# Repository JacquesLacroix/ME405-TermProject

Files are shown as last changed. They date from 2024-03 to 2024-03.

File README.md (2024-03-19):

<h1>ME 405 Term Project</h1>
<h3>Scott Frizzell & Jacques Lacroix</h3>

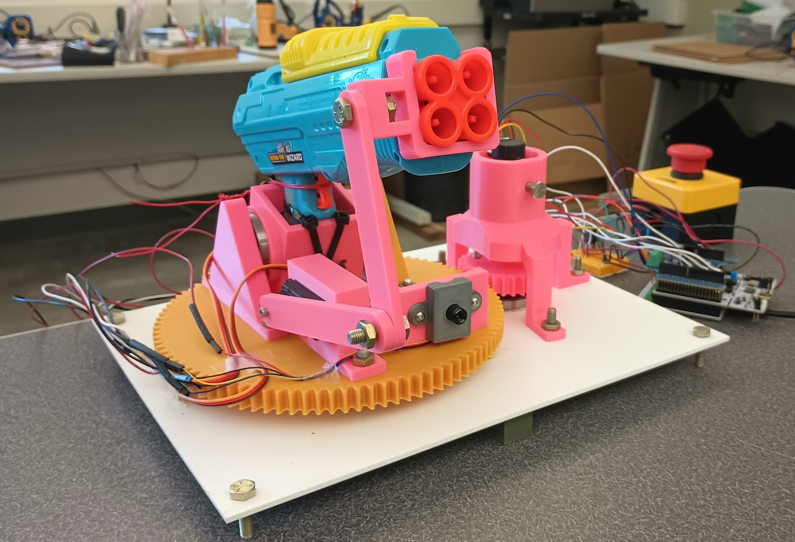
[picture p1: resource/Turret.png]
Picture of Turret


This thermal tracking, automated NERF™ turret was designed for the Department of Foamland Security. Its primary purpose is to engage in autonomous defense.

The turret's design revolves around a pump-action NERF™ gun mounted to a 2-axis mount, allowing it to shoot in nearly any direction. The mechanism uses a brushed DC motor to control the panning motion of the gun, while a servo controls the tilting motion of the gun. A servo is used to actuate the trigger mechanism, and a thermal camera is used for tracking.

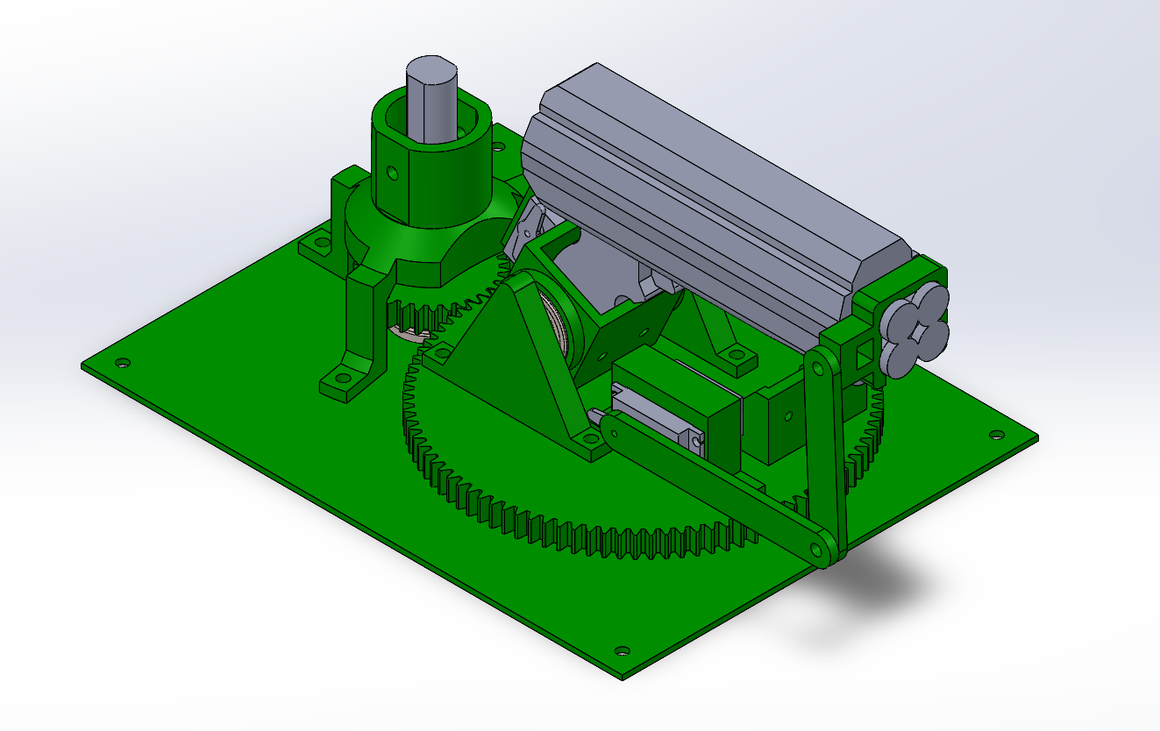
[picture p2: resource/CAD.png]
CAD model of Turret


The turret uses a gear train to reduce the motor speed and increase torque to allow the gun to swivel smoothly. Multiple tooth ratios were considered, such as 120/30, but we choose a 96/30 tooth ratio because of manufacturing constraints. 

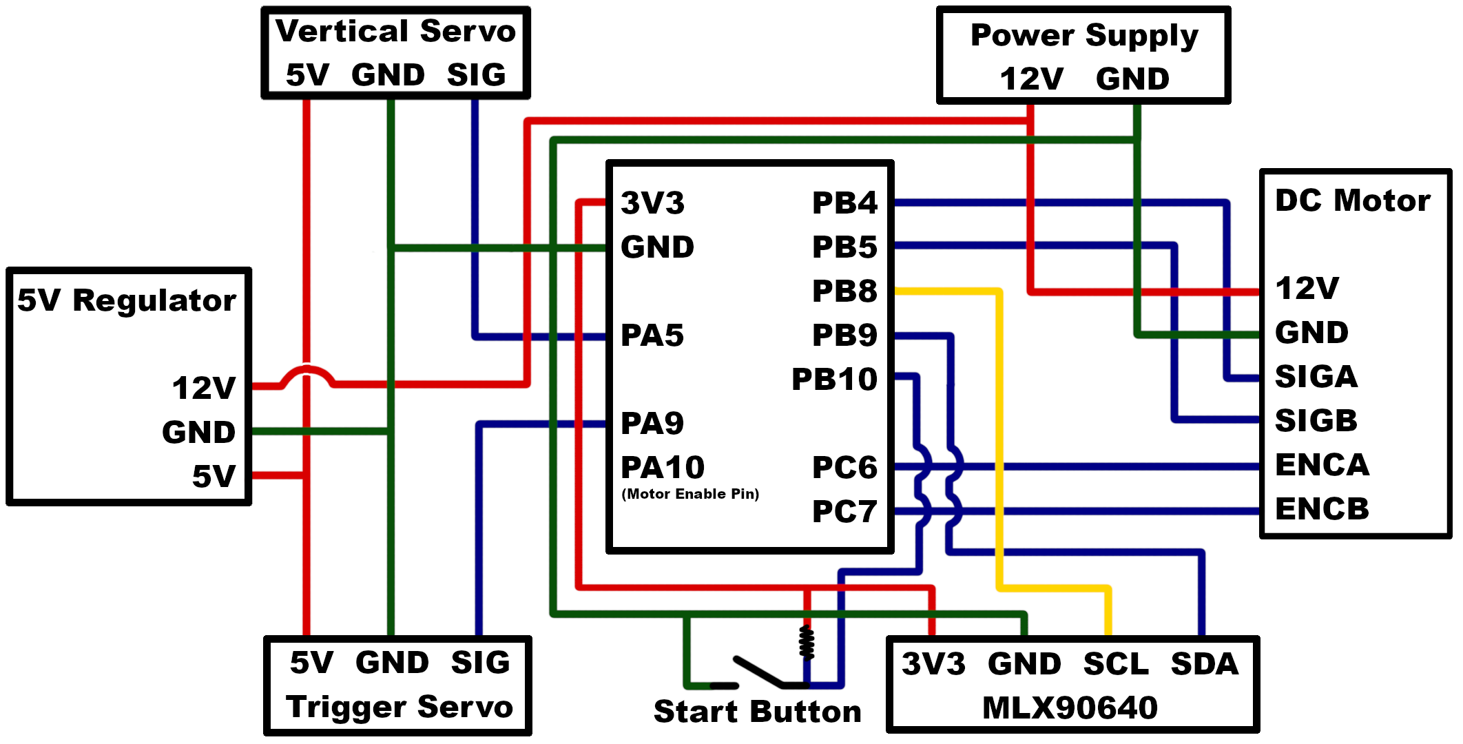
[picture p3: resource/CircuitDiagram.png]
Circuit Diagram


The device is powered by a 12V bench power supply. In our testing, the microcontroller was also be plugged into a computer. However it could be modified to take an input voltage from the bench power supply and run completely autonomously.

To power the DC motor, it was connected directly to the 12V supply. The servos only needed 5V, however, they drew too much current to simply connect them to the 5V output of the microcontroller. Instead, they were connect to the output of a 5V voltage regulator. The thermal camera was simply connected to the 3.3V output pin of the microcontroller, was it did not draw excess current.

The device is programmed using a cooperative, priority-based multitasking system, split into 5 tasks:
<ol>
    <li>Controls the panning motion of the turret.</li>
    <li>Controls the activation of the turret.</li>
    <li>Controls the tilting motion of the turret.</li>
    <li>Controls the targeting of the turret.</li>
    <li>Controls the actuation of the trigger.</li>
</ol>
Further information of the tasks and dependencies can be found here: https://jacqueslacroix.github.io/ME405-TermProject

Our primary takeaways from this design process were as follows:
<ul>
    <li>Tuning the camera parameters to accurately track targets would require additional work</li>
    <li>Tuning DC motor gains (KP, KI, KD) is a challenge, especially due to needing small changes in angle when tracking</li>
    <li>Our tracking algorithm would sometimes lock onto a target while they were moving and shoot where they used to be</li>
</ul>

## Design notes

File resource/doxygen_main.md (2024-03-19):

<h2>Scott Frizzell & Jacques Lacroix</h2>

<h3>Software Overview</h3>
The software for this project was divided into 6 main parts:
<ol>
    <li>`main.py` - The primary program responsible for controlling the rest of the software and hardware interaction</li>
    <li>`controller.py` - A PID motor controller implemented for a brushed DC motor with and encoder</li>
    <li>`motor_driver.py` - A motor driver used by the controller to interact with the DC motor</li>
    <li>`encoder_reader.py` - An encoder driver used by the controller to interact with a quadrature encoder</li>
    <li>`servo.py` - A servo driver used to control the other axis of motion and firing the weapon</li>
    <li>`mlx_cam.py` and `/mlx90640` - A wrapper class used to interact with the MLX thermal camera used for tracking</li>
</ol>

<h3>Task Overview</h3>
`main.py` was divided into 5 different tasks, each responsible for controlling a different part of the turret.

<h4>Task 1</h4>
Task 1 is responsible for controlling the turrets panning axis using the Controller class.
<ul>
    <li>State 0: Waiting for start - Waits until the start button has been pressed</li>
    <li>State 1: Idle - Waits for a new angle to be set by Task 4</li>
    <li>State 2: Panning - Runs the controller until it has reached its desired location</li>
</ul>

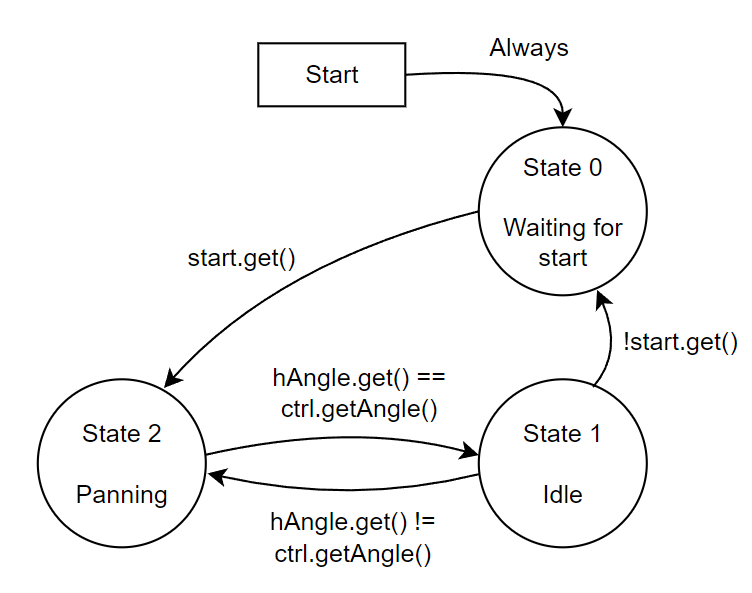
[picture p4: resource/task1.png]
Task 1 Finite State Machine Diagram


<h4>Task 2</h4>
Task 2 is responsible for starting the turret when the button is pressed.
<ul>
    <li>State 0: Waiting - Waits until the start button has been pressed</li>
    <li>State 1: Start - Waits for the turret to finish firing</li>
</ul>

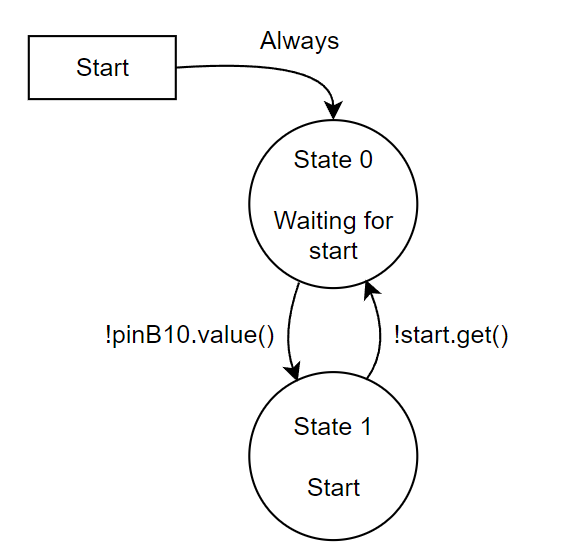
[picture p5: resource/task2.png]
Task 2 Finite State Machine Diagram


<h4>Task 3</h4>
Task 3 is responsible for controlling the tilting axis using a Servo.
<ul>
    <li>State 0: Waiting for start - Waits until the start button has been pressed</li>
    <li>State 1: Normal Operation - Sets the servo to the desired location set by Task 4</li>
</ul>

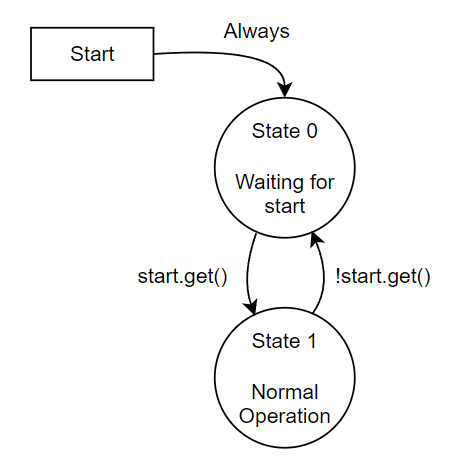
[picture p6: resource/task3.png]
Task 3 Finite State Machine Diagram


<h4>Task 4</h4>
Task 4 is responsible for interacting with the thermal camera and targeting.
<ul>
    <li>State 0: Waiting for start - Waits until the start button has been pressed</li>
    <li>State 1: Normal Operation - Takes an image when ready and sets desired angles to align turret with target</li>
</ul>

Task 4 Finite State Machine Diagram

<h4>Task 5</h4>
Task 5 is responsible for actuating the trigger mechanism.
<ul>
    <li>State 0: Waiting for start - Waits until the start button has been pressed</li>
    <li>State 1: Wait for fire - Waits for Task 4 to give the fire command</li>
    <li>State 2: Delay and reset - Pulls the trigger, waits a second, and resets the turret to run again</li>
</ul>

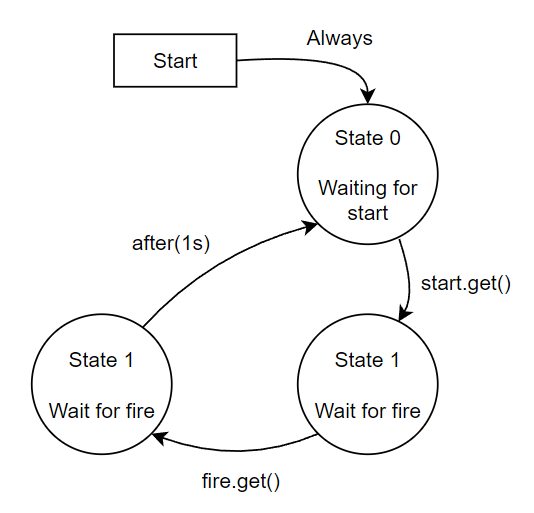
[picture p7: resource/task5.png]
Task 5 Finite State Machine Diagram


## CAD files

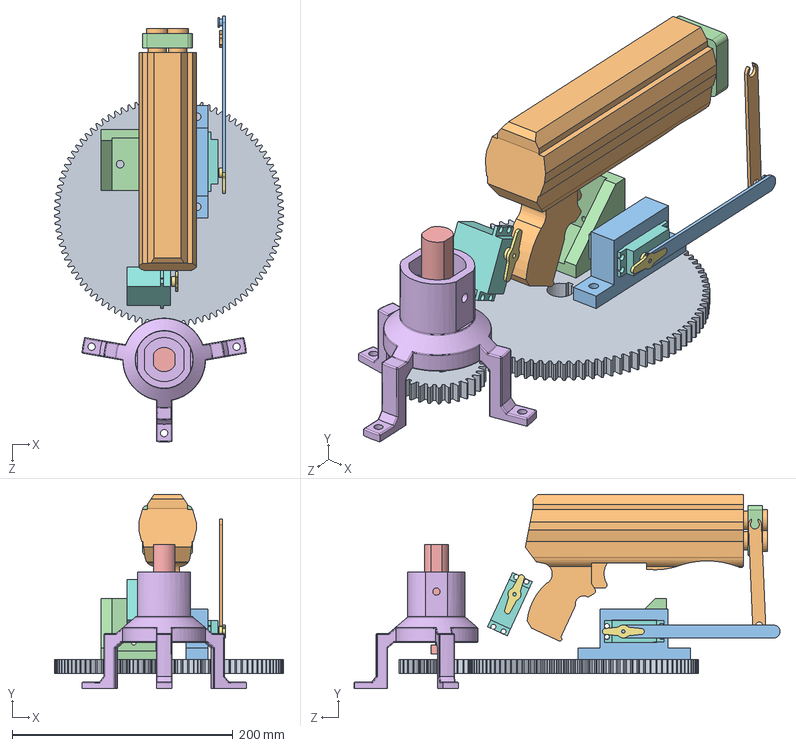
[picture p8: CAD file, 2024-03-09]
Solidworks/Assembly.SLDASM
207.4 x 175.6 x 385.6 mm
CameraMount
ServoMount
Gun
PinionLarge
Servo x 2
ServoHorn x 2
Motor Mount
Motor
GunCamConnection
CamBarServo
CamBarGun
Gear

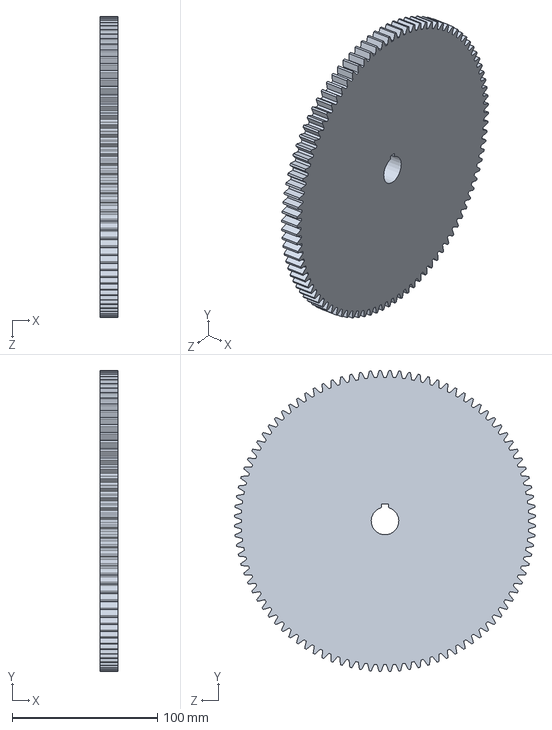
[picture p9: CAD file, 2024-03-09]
Solidworks/Gear.SLDPRT
12.7 x 207.4 x 207.4 mm

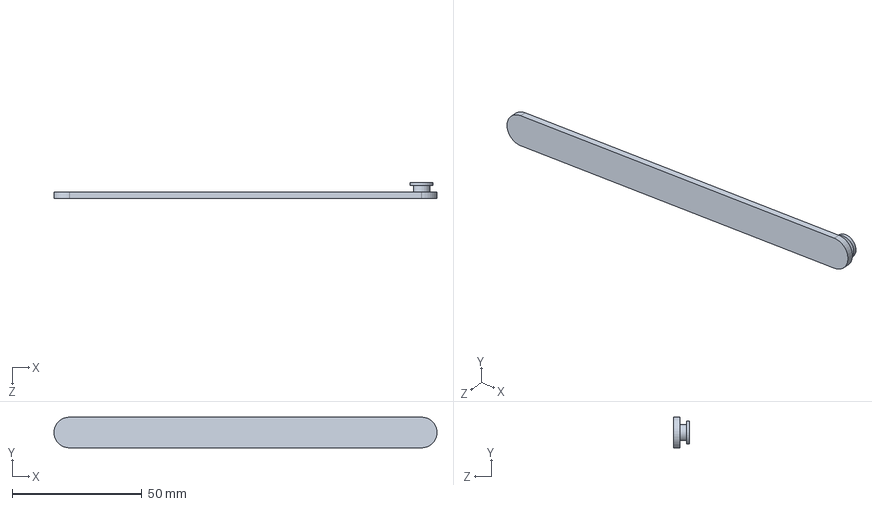
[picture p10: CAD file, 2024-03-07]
Solidworks/CamBarServo.SLDPRT
147.7 x 11.8 x 6.35 mm

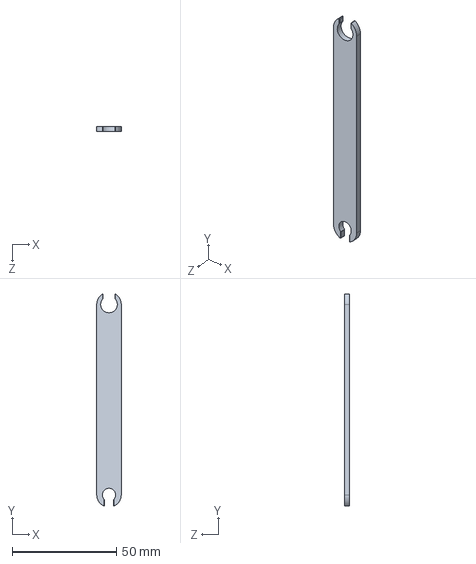
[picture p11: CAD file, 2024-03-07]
Solidworks/CamBarGun.SLDPRT
11.8 x 101.8 x 2.54 mm

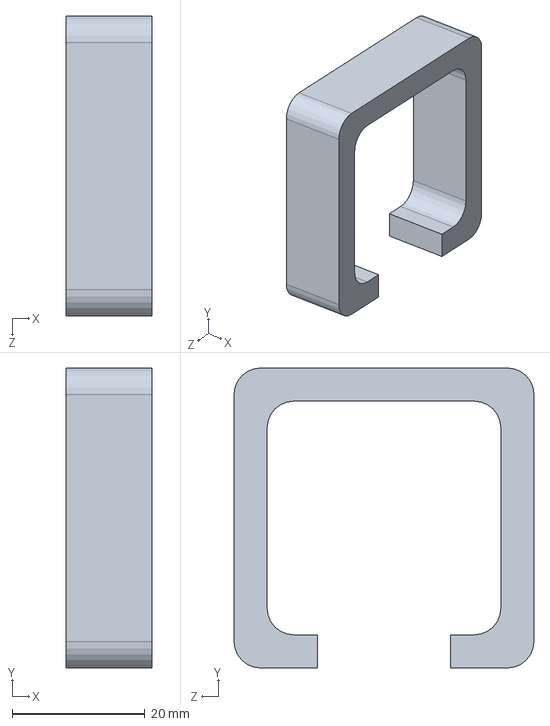
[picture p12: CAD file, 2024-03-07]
Solidworks/GunCamConnection.SLDPRT
13.0 x 45.2 x 45.2 mm

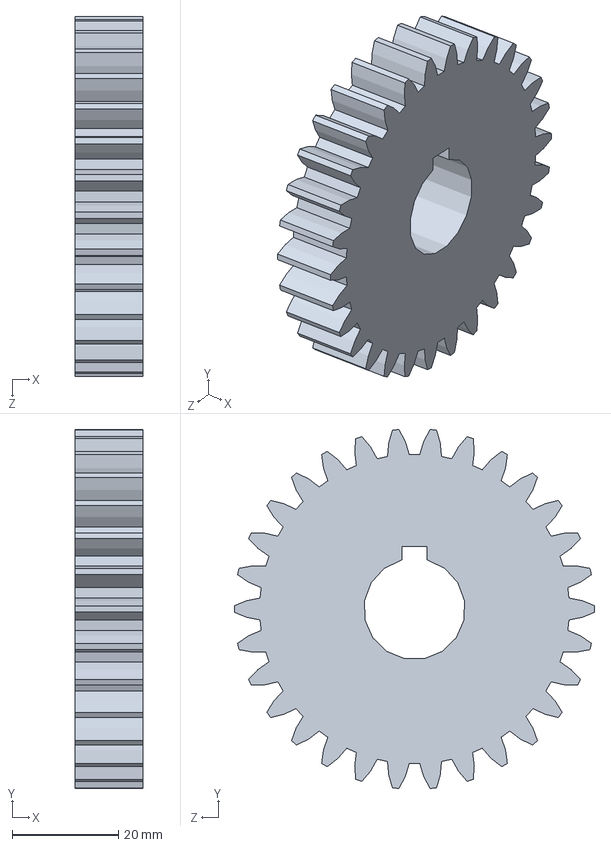
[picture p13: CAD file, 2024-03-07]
Solidworks/PinionLarge.SLDPRT
12.7 x 67.5 x 67.7 mm

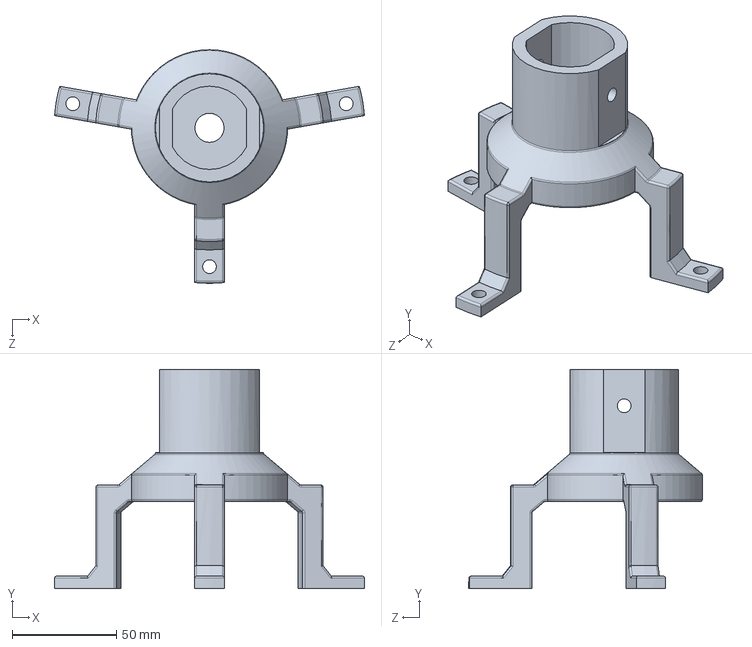
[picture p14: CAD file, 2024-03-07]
Solidworks/Motor Mount.SLDPRT
148.8 x 105.3 x 112.1 mm

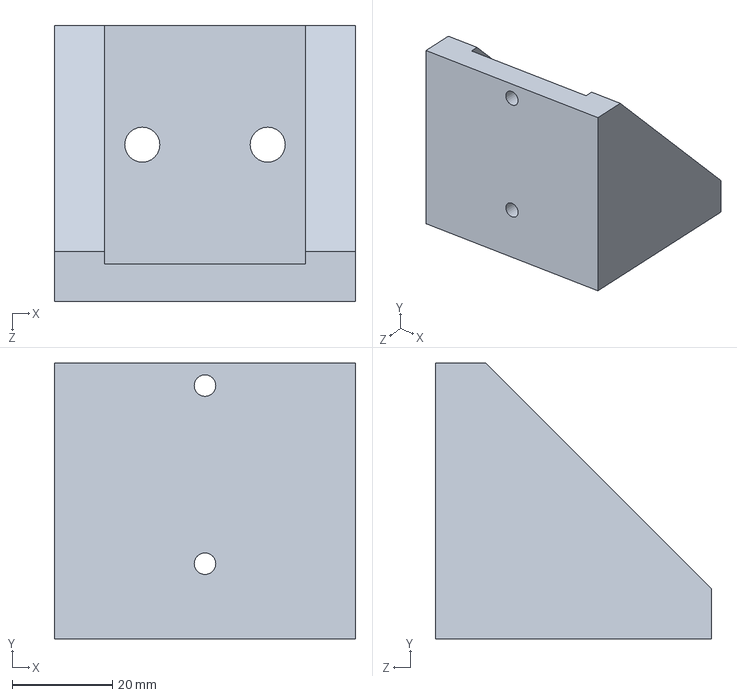
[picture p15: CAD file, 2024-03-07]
Solidworks/CameraMount.SLDPRT
60.0 x 55.0 x 55.0 mm

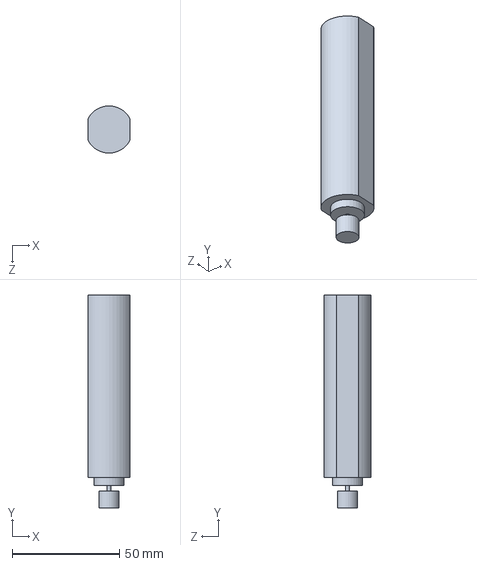
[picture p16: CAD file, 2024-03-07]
Solidworks/Motor.SLDPRT
19.5 x 99.1 x 22.0 mm

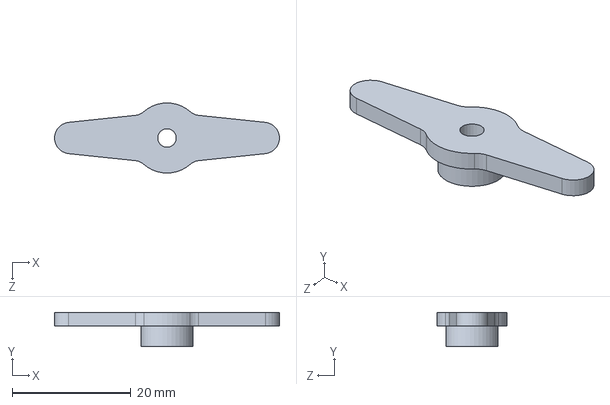
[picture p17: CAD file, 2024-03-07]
Solidworks/ServoHorn.SLDPRT
38.0 x 5.74 x 11.8 mm

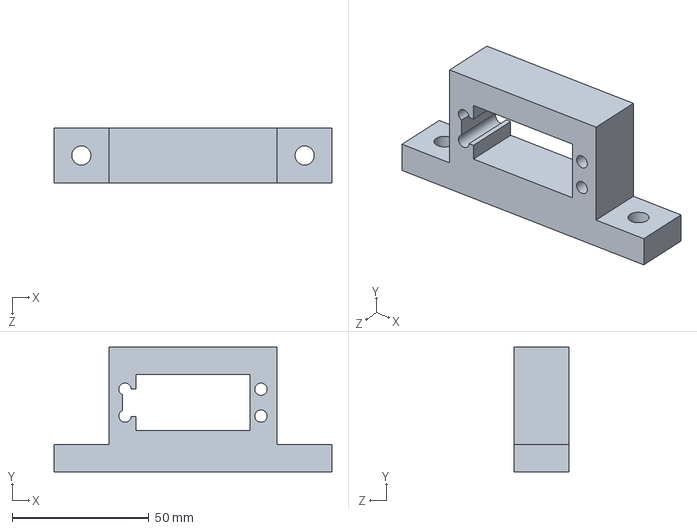
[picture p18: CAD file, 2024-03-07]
Solidworks/ServoMount.SLDPRT
101.5 x 45.5 x 20.0 mm

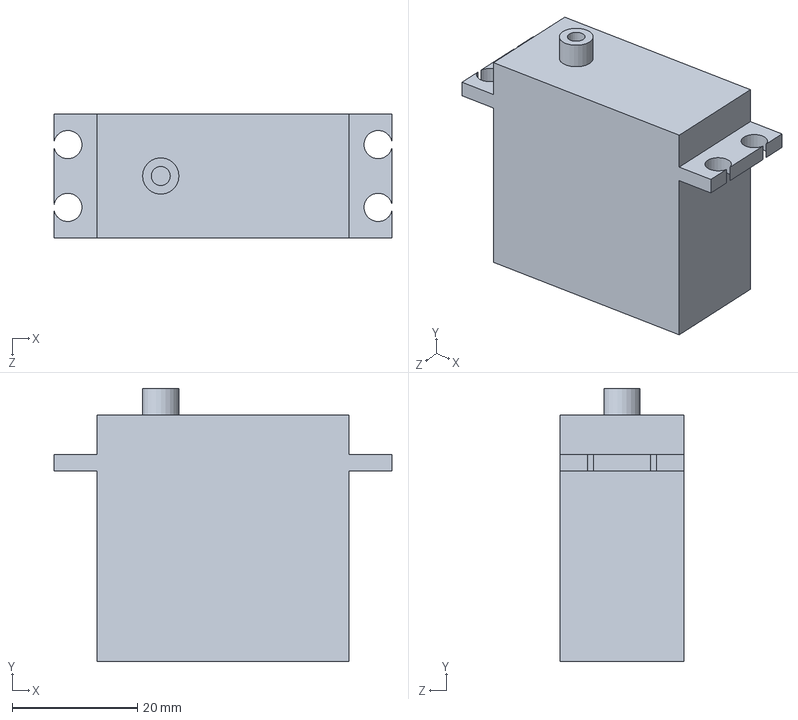
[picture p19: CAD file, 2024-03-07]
Solidworks/Servo.SLDPRT
54.0 x 43.7 x 19.8 mm

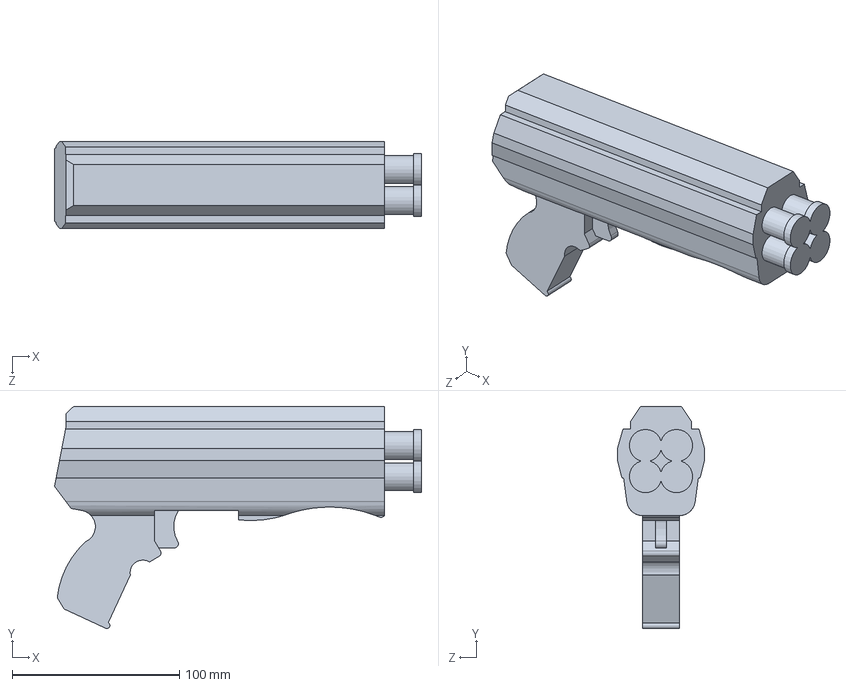
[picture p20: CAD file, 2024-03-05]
Solidworks/Gun.SLDPRT
219.4 x 132.7 x 52.1 mm

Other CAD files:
Solidworks/Base.SLDPRT
Solidworks/GunMount.SLDPRT
Solidworks/GunMountBase.SLDPRT

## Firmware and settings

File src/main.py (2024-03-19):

"""!
@file main.py
This program controls all aspects of the turret and is responsible for software and hardware interaction
"""

import pyb
import cotask
import task_share
import utime
from motor_driver import MotorDriver
from encoder_reader import Encoder
from controller import Controller
from servo import Servo
from mlx_cam import MLX_Cam
from machine import I2C
import gc

def task1(shares):
    """!
    This task handles turning the panning axis of the turret
    @param shares A tuple of shared variables between tasks
    @returns None
    """
    (hAngle, start, readyForImage, vAngle, fire) = shares

    state = 0

    hAngle.put(0)
    readyForImage.put(0)
    
    pinA10 = pyb.Pin(pyb.Pin.board.PA10, pyb.Pin.OUT_PP)
    pinB4 = pyb.Pin(pyb.Pin.board.PB4, pyb.Pin.OUT_PP) 
    pinB5 = pyb.Pin(pyb.Pin.board.PB5, pyb.Pin.OUT_PP)
    
    pinC6 = pyb.Pin(pyb.Pin.board.PC6, pyb.Pin.OUT_PP) 
    pinC7 = pyb.Pin(pyb.Pin.board.PC7, pyb.Pin.OUT_PP)
    
    tim3 = pyb.Timer(3, freq=20000)
    
    tim8 = pyb.Timer(8, prescaler=1, period=65535)
    
    motor = MotorDriver(pinA10, pinB4, pinB5, tim3)
    
    encoder = Encoder(pinC6, pinC7, tim8)
    
    ctrl = Controller(encoder, motor, 0, kp=0.06, ki=0, kd=0.0002, ticks=8000, gearRatio=float(96)/float(30))
    
    closeEnough = const(3)

    yield

    while True:
        #print(state)
        if state == 0:
            # Waiting for start
            if start.get():
                ctrl.set_kp(0.06)
                ctrl.set_kd(0.0002)
                hAngle.put(-180)
                ctrl.setAngle(hAngle.get())
                state = 2
            yield
        elif state == 1:
            # Idle
            if abs(hAngle.get() - ctrl.readAngle()) > closeEnough:      
                ctrl.setAngle(hAngle.get())
                readyForImage.put(0)
                state = 2
            elif not start.get():
                readyForImage.put(0)
                state = 0
            yield
        elif state == 2:
            # Panning
            ctrl.run()
            if abs(hAngle.get() - ctrl.readAngle()) <= closeEnough: # May need to change this
                for i in range(3):
                    ctrl.run()
                ctrl.motor.set_duty_cycle(0)
                ctrl.set_kp(0.2)
                ctrl.set_kd(0.01)
                if start.get():
                    readyForImage.put(1)
                    state = 1
                else:
                    state = 1
            yield
        else:
            raise ValueError(f"Invalid Task 1 State: {state}")

def task2(shares):

    """!
    This task handles the start button
    @param shares A tuple of shared variables between tasks
    @returns None
    """
    (hAngle, start, readyForImage, vAngle, fire) = shares

    start.put(0)

    state = 0

    pinB10 = pyb.Pin(pyb.Pin.board.PB10, pyb.Pin.IN)
    
    counter = 0

    yield

    while True:
        if state == 0:
            # Waiting
            if not pinB10.value():
                start.put(1)
                fire.put(0) 
                state = 1
                counter = 0
            yield 
        elif state == 1:
            # Start
            if not start.get():
                state = 0
            yield
        else:
            raise ValueError(f"Invalid Task 2 State: {state}")

def task3(shares):
    """!
    This task handles turning the vertical axis of the turret
    @param shares A tuple of shared variables between tasks
    @returns None
    """
    (hAngle, start, readyForImage, vAngle, fire) = shares

    state = 0

    vAngle.put(45)

    pinA5 = pyb.Pin(pyb.Pin.board.PA5, pyb.Pin.OUT_PP)
    timer2 = pyb.Timer(2, freq=50)
    t2ch1 = timer2.channel(1, pyb.Timer.PWM, pin=pinA5)
    vServo = Servo(t2ch1, angle=vAngle.get(), minAngle=45, maxAngle=60)

    yield

    while True:
        if state == 0:
            # Waiting for start
            if start.get():
                state = 1
            yield
        elif state == 1:
            # Normal Operation
            if vAngle.get() != vServo.read():
                vServo.write(vAngle.get())
                yield
            if not start.get():
                state = 0
            yield
        else:
            raise ValueError(f"Invalid Task 3 State: {state}")

def task4(shares):
    """!
    This task handles taking images and setting angles
    @param shares A tuple of shared variables between tasks
    @returns None
    """
    (hAngle, start, readyForImage, vAngle, fire) = shares

    state = 0

    fire.put(0)

    pinB8 = pyb.Pin(pyb.Pin.board.PB8, pyb.Pin.ALT, alt=4)
    pinB9 = pyb.Pin(pyb.Pin.board.PB9, pyb.Pin.ALT, alt=4)
    i2c = I2C(1)
    camera = MLX_Cam(i2c)
    image = None
    arrayImage = []
    vMax = 0
    hMax = 0
    
    hOffset = const(-10)
    vOffset = const(-16)
    hScale = const(0.95)
    vScale = const(1)

    yield

    while True:
        if state == 0:
            # Waiting for start
            if start.get():
                state = 1
            yield
        elif state == 1:
            # Normal Operation
            if readyForImage.get():
                while not image:
                    image = camera.get_image_nonblocking()
                    yield
                for line in camera.get_csv(image):
                    arrayImage.append(line.split(","))
                    yield
                for (hIdx, line) in enumerate(arrayImage):
                    if hIdx < 4:
                        continue
                    for (vIdx, pixel) in enumerate(line):
                        try:
                            if float(pixel) > float(arrayImage[hMax][vMax]):
                                vMax = vIdx
                                hMax = hIdx
                        except:
                            raise ValueError("Camera returned non-number data")
                    yield
                
                hNew = int(hAngle.get() + hScale*(hMax + hOffset))
                vNew = int(vScale*(max(vMax, 16) + vOffset) + 43)
                
                print("-------Next--------")
                print("Maximum Heat Signature:")
                print(hMax)
                print(vMax)
                print("Pointing at:")
                print(hAngle.get())
                print(vAngle.get())
                print("Where to go:")
                print(hNew)
                print(vNew)
                
                if abs(hNew - hAngle.get()) <= 1 and abs(vNew - vAngle.get()) <= 1:
                    fire.put(1)
                    print("Fire!")
                else:
                    hAngle.put(hNew)
                    vAngle.put(vNew)
                image = None
                arrayImage = []
                vMax = 0
                hMax = 0
                state = 0
                
            yield
            
        else:
           raise ValueError(f"Invalid Task 4 State: {state}") 

def task5(shares):
    """!
    This task handles actutating the trigger
    @param shares A tuple of shared variables between tasks
    @returns None
    """
    (hAngle, start, readyForImage, vAngle, fire) = shares

    state = 0

    pinA9 = pyb.Pin(pyb.Pin.board.PA9, pyb.Pin.OUT_PP)
    timer1 = pyb.Timer(1, freq=50)
    t1ch2 = timer1.channel(2, pyb.Timer.PWM, pin=pinA9)
    aServo = Servo(t1ch2, angle=30, maxAngle=120)

    counter = 0

    yield

    while True:
        if state == 0:
            # Waiting for start
            if start.get():
                counter = 0
                state = 1
            yield
        elif state == 1:
            # Wait for fire
            if counter < 25:
                counter += 1
            else:
                if fire.get():
                    aServo.write(120)
                    fire.put(0)
                    state = 2
            yield
        elif state == 2:
            # Delay and reset
            if counter > 5:
                print("Done!")
                aServo.write(30)
                counter = 0
                start.put(0)
                hAngle.put(0)
                vAngle.put(45)
                readyForImage.put(0)
                state = 0
            else:
                counter += 1
            yield
        else:
            raise ValueError(f"Invalid Task 5 State: {state}")

if __name__ == "__main__":
    shareList = [
        task_share.Share("i", name="hAngle"),
        task_share.Share("b", name="start"),
        task_share.Share("b", name="ReadyForImage"),
        task_share.Share("i", name="vAngle"),
        task_share.Share("b", name="Fire")
    ]
    
    tasks = [
        cotask.Task(task1, name="Task 1", priority=2, period=10, shares=shareList),
        cotask.Task(task2, name="Task 2", priority=1, period=200, shares=shareList),
        cotask.Task(task3, name="Task 3", priority=0, period=100, shares=shareList),
        cotask.Task(task4, name="Task 4", priority=0, period=10, shares=shareList),
        cotask.Task(task5, name="Task 5", priority=0, period=200, shares=shareList),
    ]

    for task in tasks:
        cotask.task_list.append(task)

    while True:
        cotask.task_list.pri_sched()

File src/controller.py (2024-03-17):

"""! 
@file controller.py
Implements a porportional gain controller for a DC motor with a quadrature encoder
"""
import encoder_reader
import motor_driver
import utime

class Controller:
    """!
    This class implements a proportional gain controller for a DC motor with quadrature encoder
    """
    def __init__(self, encoder, motor, setpoint, kp, ki, kd, ticks=8000, gearRatio=1):
        """!
        Create a DC motor controller object with proportional gain from quadrature encoder feedback
        @param encoder The encoder object used to measure position
        @param motor The motor driver used to send signals to the motor
        @param setpoint The target position for the motor to turn to
        @param kp The proportional gain coefficient for the controller to use
        @param ki The integral gain coefficient for the controller to use
        @param kd The derivative gain coefficient for the controller to use
        @param ticks The number of encoder ticks corresponding to 1 full rotation
        @param gearRatio The gear speed reduction ratio, allowing for angles to be set on the output shaft (Output Gear Teeth/Motor Pinion Teeth).
        A positive ratio should be used for odd numbers of gears, and a negative ratio should be used for even numbers of gears to ensure the output
        shaft rotates in the desired direction. The ratio should be negated if the motor is mounted upside-down relative to the output shaft.
        @returns Controller
        """
        self.encoder = encoder
        self.motor = motor
        self.set_setpoint(setpoint)
        self.set_kp(kp)
        self.set_ki(ki)
        self.set_kd(kd)
        self.ticks = ticks
        self.gearRatio = gearRatio
        self.eSum = 0
        self.last = 0
        
    def run(self):
        """!
        Runs one step of the control loop. Changes motor's pulse width and logs the current time and encoder position
        @returns None
        """
        position = self.encoder.read()
        self.error = self.setpoint - position
        PWM = self.kp*self.error + self.ki*self.eSum + self.kd*(self.error - self.last)
        # self.eSum += self.error
        self.last = self.error
        self.motor.set_duty_cycle(PWM)
        return PWM
    
    def set_setpoint(self, setpoint):
        """!
        Allows the user to change the motor's target position
        @param setpoint The position for the motor to turn to
        @returns None
        """
        self.setpoint = setpoint

    def setAngle(self, angle):
        """!
        Allows the user to input a desired angle on the output shaft
        @param angle The desired output shaft angle
        @returns None
        """
        self.setpoint = self.angleToTicks(angle)

    def readAngle(self):
        """!
        Allows the user to read the current angle of the output shaft
        @returns int
        """
        return self.ticksToAngle(self.encoder.read())
        
    def set_kp(self, kp):
        """!
        Allows the user to change the controller's porportional gain coefficent
        @param kp The Kp value to set the controller's proportional gain to
        @returns None
        """
        self.kp = kp
        
    def set_ki(self, ki):
        """!
        Allows the user to change the controller's integral gain coefficent
        @param ki The Ki value to set the controller's integral gain to
        @returns None
        """
        self.ki = ki
        
    def set_kd(self, kd):
        """!
        Allows the user to change the controller's derivative gain coefficent
        @param kd The Kd value to set the controller's derivative gain to
        @returns None
        """
        self.kd = kd

    def angleToTicks(self, angle):
        """!
        Converts a specified angle into a encoder ticks
        @param angle The angle to be converted
        @returns int
        """
        return angle * self.ticks * self.gearRatio / 360

    def ticksToAngle(self, ticks):
        """!
        Converts a specified number of encoder ticks into an angle
        @param ticks The number of ticks to be converted
        @returns int
        """
        return ticks * 360 // (self.ticks * self.gearRatio)
    
if __name__ == "__main__":
    
    pinC1 = pyb.Pin(pyb.Pin.board.PC1, pyb.Pin.OUT_PP)
    pinA0 = pyb.Pin(pyb.Pin.board.PA0, pyb.Pin.OUT_PP) 
    pinA1 = pyb.Pin(pyb.Pin.board.PA1, pyb.Pin.OUT_PP)
    
    pinC6 = pyb.Pin(pyb.Pin.board.PC6, pyb.Pin.OUT_PP) 
    pinC7 = pyb.Pin(pyb.Pin.board.PC7, pyb.Pin.OUT_PP)
    
    tim5 = pyb.Timer(5, freq=20000)   #Motor Controller Timer 
    tim8 = pyb.Timer(8, prescaler=1, period=65535)
    
    motor = motor_driver.MotorDriver(pinC1, pinA0, pinA1, tim5)
    encoder = encoder_reader.Encoder(pinC6, pinC7, tim8)
    
    setpoint = 1600
    
    controller = Controller(encoder, motor, setpoint, 1/16)
    
    while True:
        
        kp = input("ENTER KP VALUE: ")
        try:
            kp = float(kp)
        except:
            print("KP MUST BE NUMBER, DUMB DUMB")
            continue
        
        controller.set_kp(kp)
        encoder.zero()
        
        startticks = utime.ticks_ms()
        
        while not abs(controller.run()) < 10:        
            utime.sleep_ms(10)
        
        controller.print_list(startticks)

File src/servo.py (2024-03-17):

"""!
@file servo.py
Implements a Positional Servo wrapper class
"""

import pyb

class Servo:
    def __init__(self, timerChannel, minAngle=0, maxAngle=90, angle=0):
        """!
        Creates a Servo wrapper class
        @param timerChannel The pyb.Timer object corresponding to the signal wire output pin
        @param minAngle The minimum allowable angle the servo can be set to
        @param maxAngle The maximum allowable angle the servo can be set to
        @param angle The angle the servo should be initialized to
        """
        self.channel = timerChannel
        self.minAngle = minAngle
        self.maxAngle = maxAngle
        self.write(angle)

    def write(self, angle):
        """!
        This method sets the servo to a specified angle
        @param angle The desired angle
        @returns None
        """
        self.angle = angle
        self.channel.pulse_width_percent(2.5 + 5*max(self.minAngle, min(angle, self.maxAngle))/90)

    def read(self):
        """!
        This method returns the angle that the servo is set to
        @returns int
        """
        return self.angle

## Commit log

2024-03-03 Create Solidworks Folder
    [CameraMount.SLDPRT, ServoMount.SLDPRT]
2024-03-03 Create assembly
    [CameraMount.SLDPRT, ServoMount.SLDPRT]
2024-03-05 Solidworks Assembly Update
    [Assembly.SLDASM, Gear.SLDPRT, Gun.SLDPRT]
2024-03-05 Update Gears
    [Assembly.SLDASM, Gear.SLDPRT, GearLarge.SLDPRT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]
2024-03-06 Update Pinion
    [Assembly.SLDASM, PinionLarge.SLDPRT]
2024-03-07 Update Gear
    [Assembly.SLDASM, GearLarge.SLDPRT, PinionLarge.SLDPRT]
2024-03-07 Update Servo Mount
    [Assembly.SLDASM, ServoMount.SLDPRT]
2024-03-07 Add Servo
    [Assembly.SLDASM]
2024-03-07 Add missing files
    [GunMount.SLDPRT, Servo.SLDPRT, ServoHorn.SLDPRT]
2024-03-07 Solidworks update
    [Assembly.SLDASM, Base.SLDPRT, CamBarGun.SLDPRT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]
2024-03-07 Update GunMount
    [Assembly.SLDASM, GunMount.SLDPRT]
2024-03-07 Solidworks done (definitely real)
    [Assembly.SLDASM, Base.SLDPRT, CamBarGun.SLDPRT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]
2024-03-07 Remove Excess Files
    [Assembly.SLDASM, Gear.SLDPRT, Pinion.SLDPRT]
2024-03-08 getting the ******* servo to work
    [GearLarge.SLDPRT]
2024-03-08 Work on main and servo
2024-03-09 Make smaller gear
    [Assembly.SLDASM, Base.SLDPRT, Gear.SLDPRT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]
2024-03-11 Fix gear ratio
2024-03-12 Create desktop.py and allow multiple runs without reset
    [main.py]
2024-03-12 Work on camera code
2024-03-14 brain melting calibration
2024-03-17 Start documentation
    [GearLarge.SLDPRT, GearShaft.SLDPRT]
